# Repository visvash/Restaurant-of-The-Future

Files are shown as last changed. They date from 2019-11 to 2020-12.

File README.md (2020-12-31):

# Restaurant-of-The-Future
Restaurant of the Future: <a href="https://www.facebook.com/marsiitr/videos/214354466310067/">Facebook</a> / <a href = "https://www.youtube.com/watch?v=dR3jsaHACXw">Youtube</a>
## The Waiter Robot
> Hello,
> I have Re-designed an improved version of the robotic waiter, capable of traversing in a restaurant <b>autonomously</b> with a 3WD.
> I applied a Lead-screw based mechanism to Al-extrusions to carry and transfer <b>payloads</b> up to 10kg to variable platforms.
> It has incorporated general curve navigation with the help of encoder coupled motor and PID controller for navigation.
---
## Mechanical Design
Design: ROTF Robot<br>
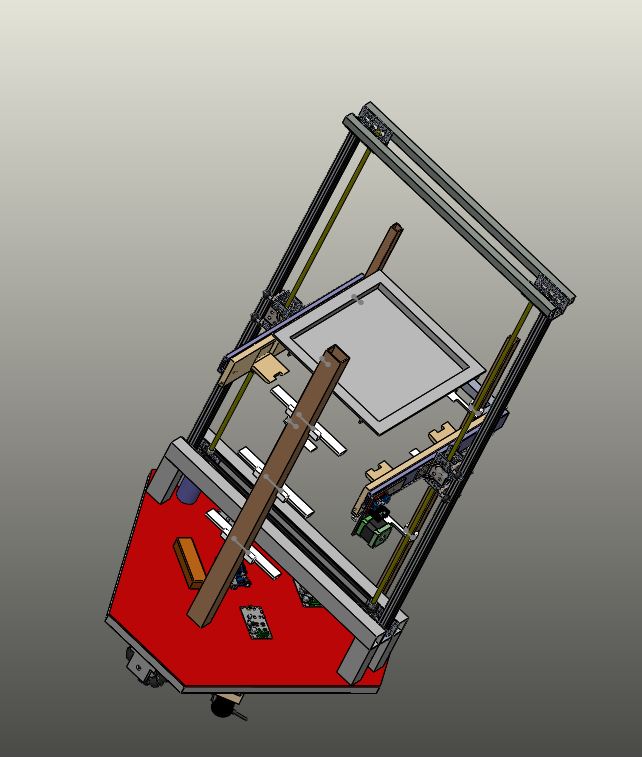
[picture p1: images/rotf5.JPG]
<br>
3 Wheel Omni Drive For Traversing<br>
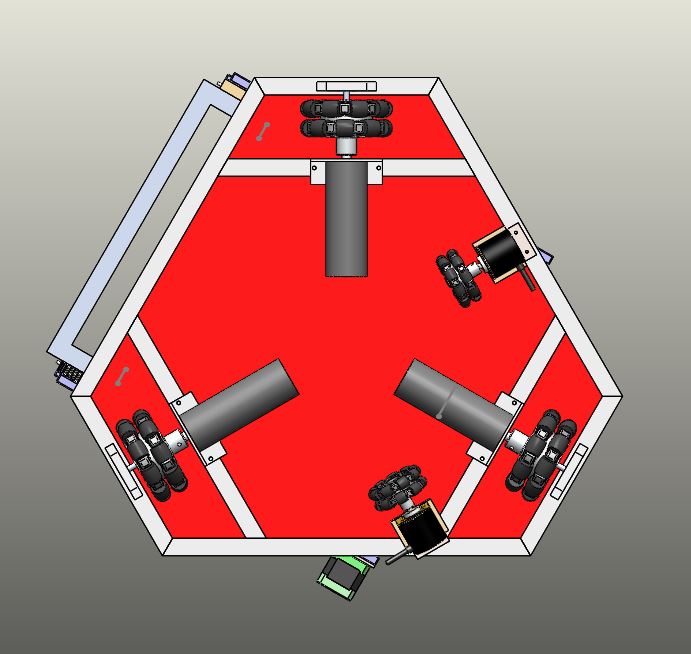
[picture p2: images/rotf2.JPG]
<br>
Extrusion Rails Using Lead-Screw Mechanism<br>
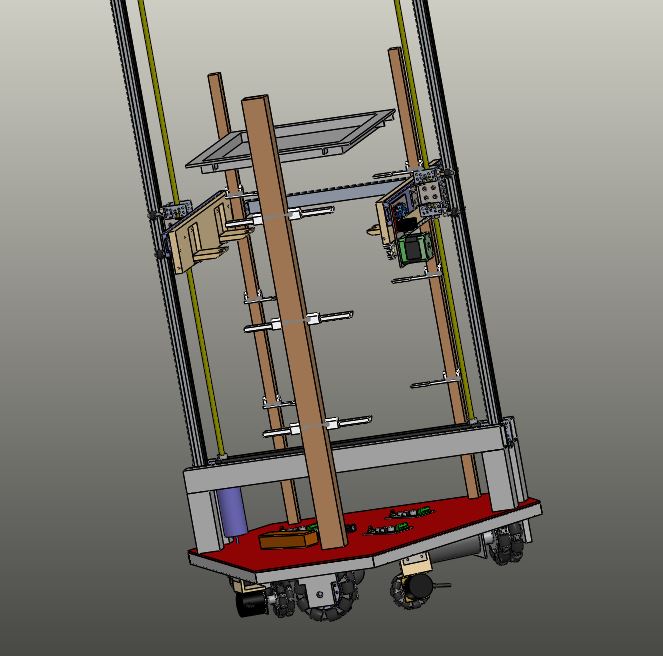
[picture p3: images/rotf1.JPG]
<br>
# Electronics and control
## Process brief
<ol>
<li>Image Input from the overhead cameras on the restaurant are processed and path is planned using Image Processing and Dijkstra Algorithm.</li>
<li>Path send to Arduino using Wifi Module</li>
<li>Omni chasis based traversal on the given path of the bot to reach the desired table.</li>
<li>Chatbot starts interacting with the the customer and takes the order while recognising face and emotion of the customer.</li>
<li>After taking order, Bot traverses back to the initial position, waits for the order to be kept on its serving trays.</li>
<li>Bot traverses back to the customer on the same path and serves using a 3-tray serving mechanism</li>
</ol>

### Path Planning and Navigation
<ol>
<li><a href =" ">Image</a> is resized to (300 * 300) pixels (<a href = " ">sample resized</a>) and edge detection is deployed on grey image (<a href = " ">sample</a>).</li>
<li>Closed objects are assigned white pixel value. Fractal concept deployed for the same(<a href = " ">sample</a>).</li>
<li>Image is smoothened(<a href = " ">sample</a>).</li>
<li>Divided into a (n*n) grid with grid size (d*d), here n = 30, d= 10 (<a href = " ">sample Grids.txt</a>). </li>
<li>Each grid is declared as an obstacle(value =0) or a path(value =1) depending of the threshold value of the white pixel count.</li>
<li>Grid generated is written in a file and is the input to the shortest path planning - Dijkstra Algorithm(<a href = " ">src code</a>). Each unit of the grid in considered as the vertic and adajent vertics are analysed of each unit to generate a matrix of all vertices. </li>
<li>"Srcdest.txt" file stores the planned path in the form of vertices to traverse on(<a href = " ">sample</a>).</li>
<li>Path string, for instance R2F2B1L1, meaning to move 2 step to the right, 2 step forward, 1 step backward, 1 step Left, is generated by reading vertices.  </li>
<li>Path string is send using the urllib library of python on the url of the esp8266 Wifi module, obtained by connecting PC and Module on the same network.</li>
</ol>
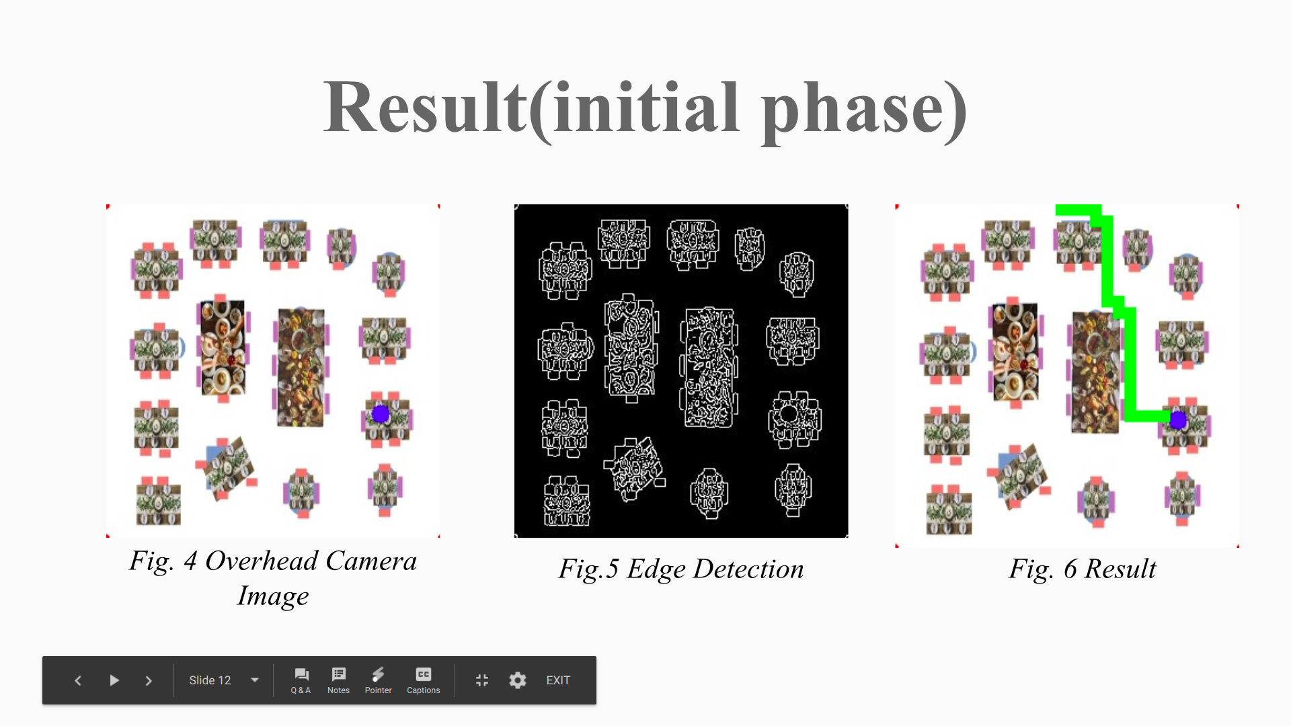
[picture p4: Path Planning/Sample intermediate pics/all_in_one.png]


### Omni chasis based motion control
<ol>
<li>Path is received using an ESP module in form of string giving units of motion in each direction. The end of path is detected by adding a letter 'e' at end of each string.</li>
<li>Each unit length of string is mapped with some unit on ground using an encoder.</li>
<li>A gyro and PID is used to avoid any rotation about its axis. Encoders and PID are used to avoid any drift.</li>
<li>Once reached the destination, it sends a signal to the head and head motion starts.</li>
<li>After getting signal from the head a "reverse" function reverses the string and adds an 'e' at the end to make the bot retrace the path back.</li>
<li>Cytron motor drivers are used for all three motors of the chassis.</li>
</ol>

### Interaction Aspect
Raspberry Pi act as a central processing system for the bot to recognise customers face and align the head accordingly using servo motors, greet and take order using Chatbot API.

### 3-Tray Serving Mechanism
<ol>
<li>After reaching the customer in mode 2, the tray motion gets activated.</li>
<li>The lifting mechanism uses dc motors and encoders, whereas the front-back motion uses stepper motor.</li>
<li>Using encoders we map the units with distance it has to traverse to reach each of the trays.</li>
<li>On reaching the tray, the front-back mechanism gets activated.</li>
<li>The number of units the stepper have to move in front and back is mapped using the standard Stepper motor library.</li>
<li>The lifting mechanism is carried by DC motors and Cytron motor driver whereas the front-back motion is supported by the stepper motors and the NEX motor driver.</li>
</ol>

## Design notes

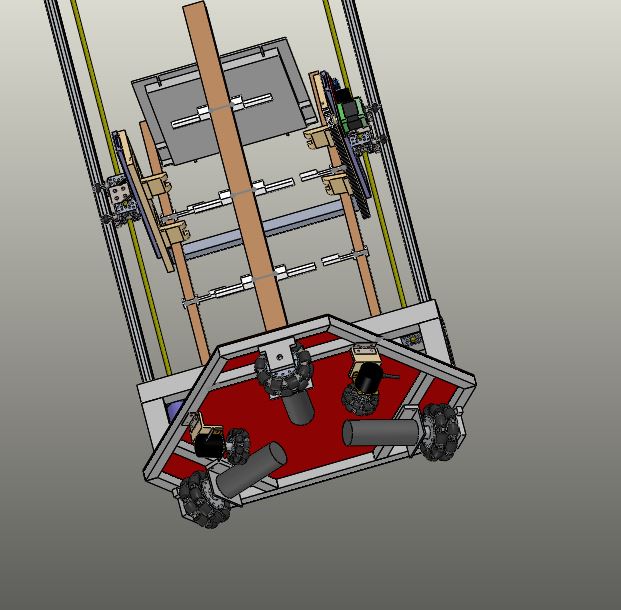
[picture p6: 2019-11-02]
images/rotf6.JPG

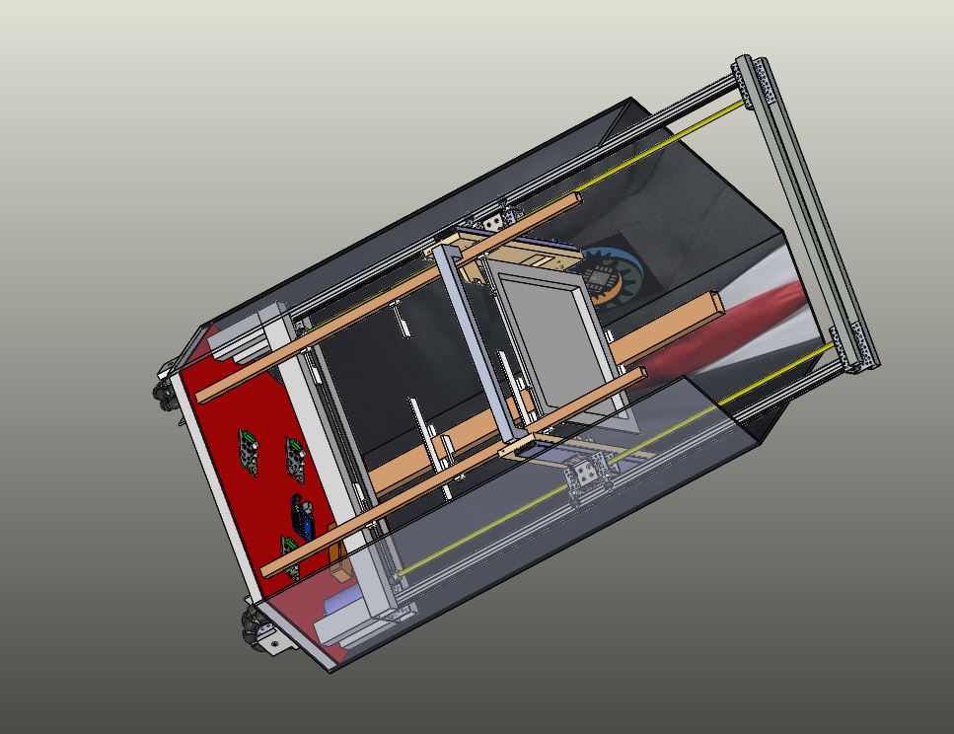
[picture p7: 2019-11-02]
images/rotf7.JPG

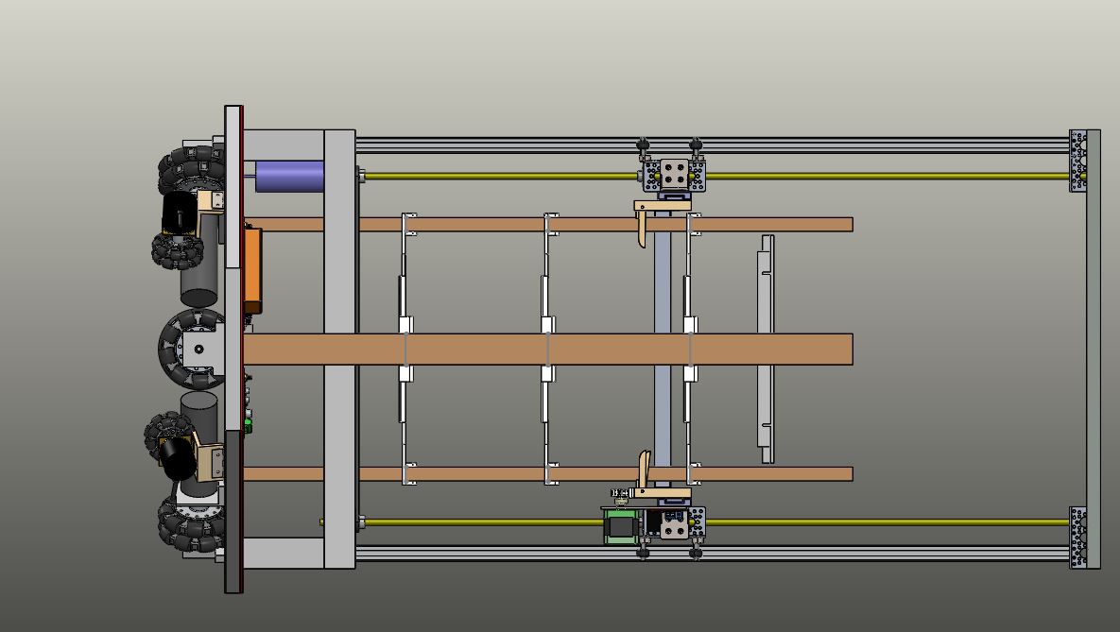
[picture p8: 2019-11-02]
images/rotf4.JPG

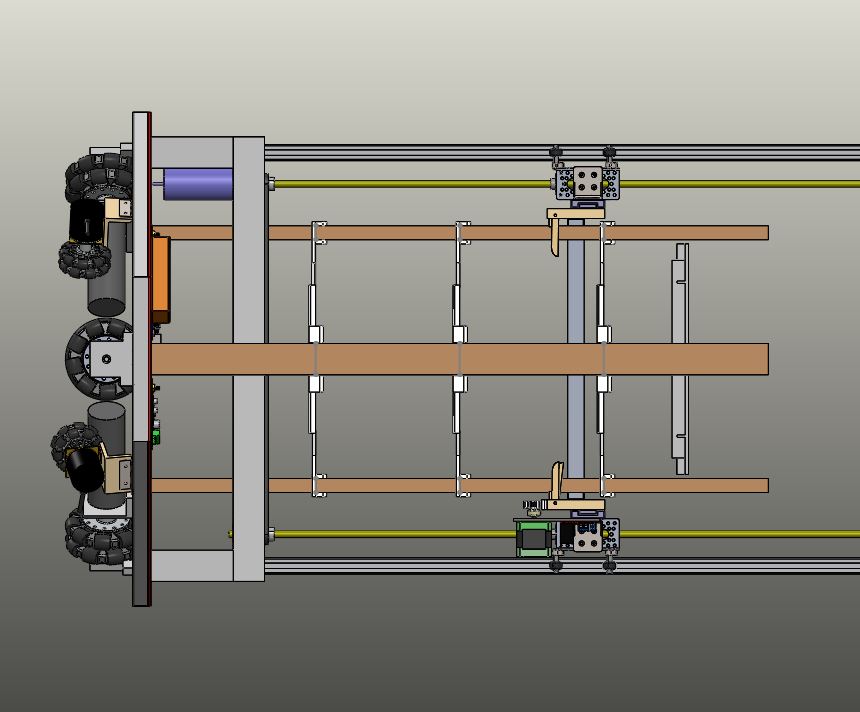
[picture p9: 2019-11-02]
images/rotf3.JPG

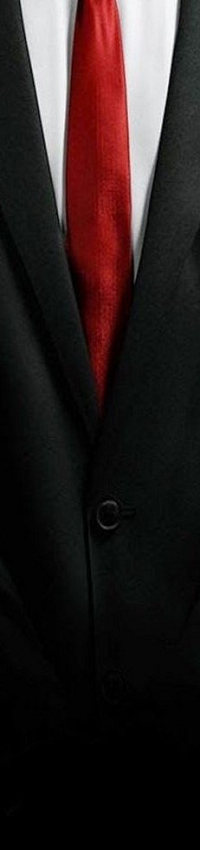
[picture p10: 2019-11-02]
ROTFnew/row-1-col-2.png

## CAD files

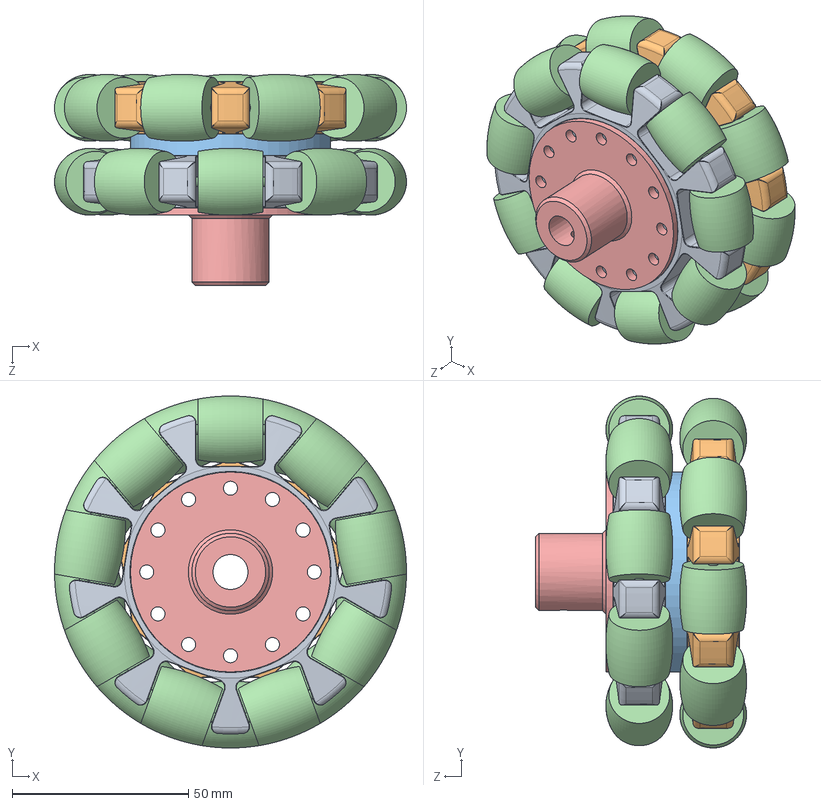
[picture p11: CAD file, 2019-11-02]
ROTFnew/OmniChasssis/OmniWheel/banhxe.SLDASM
100.0 x 100.0 x 60.0 mm
omniwheel_1
omniwheel_2
Part1^banhxe
roller x 18
Part3^banhxe

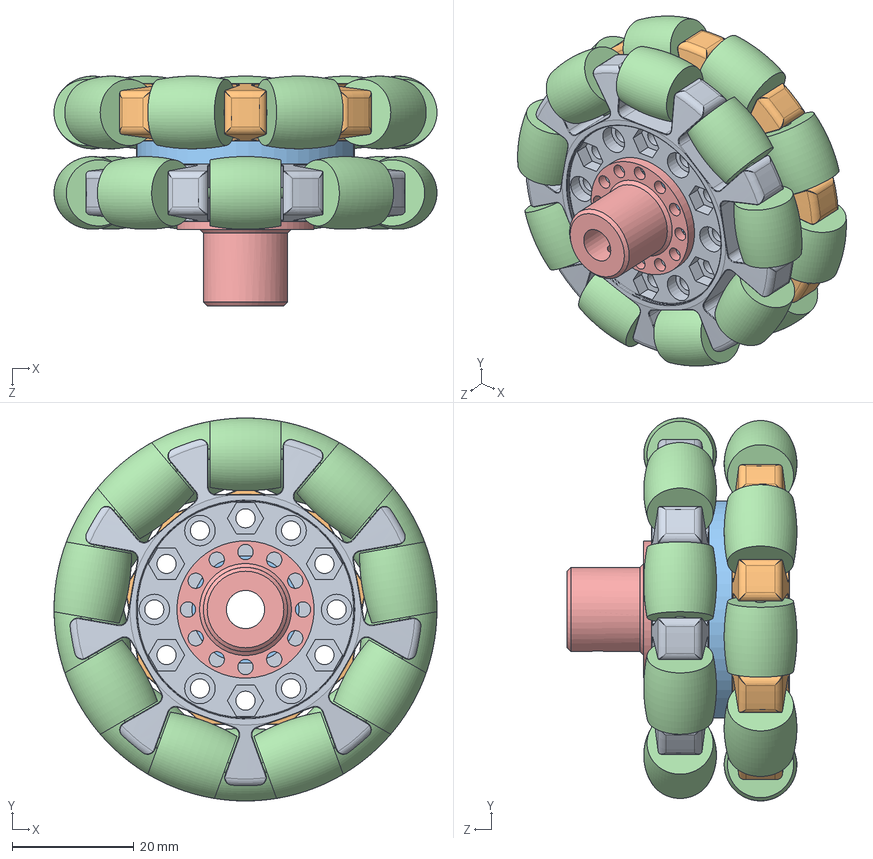
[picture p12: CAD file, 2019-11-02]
ROTFnew/OmniChasssis/OmniWheel_Encoder/banhxe.SLDASM
63.0 x 63.0 x 37.8 mm
omniwheel_1
omniwheel_2
Part1^banhxe
roller x 18
Part3^banhxe

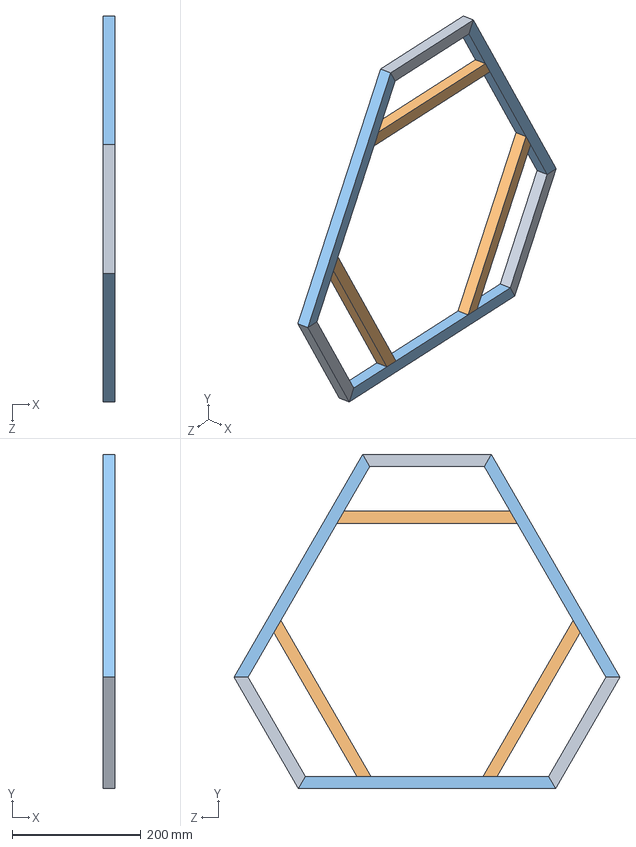
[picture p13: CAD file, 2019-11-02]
ROTFnew/OmniChasssis/OmniFrame.SLDASM
19.0 x 519.6 x 600.0 mm
Channel_200mm x 3
Channel_280mm x 3
Channel_400mm x 3

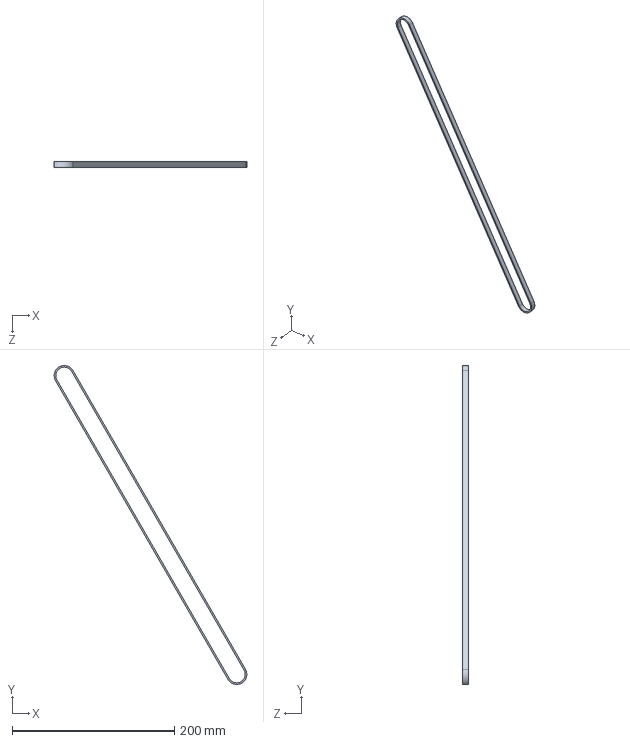
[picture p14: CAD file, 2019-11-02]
ROTFnew/Belt1-4.sldprt
237.9 x 393.7 x 7.00 mm

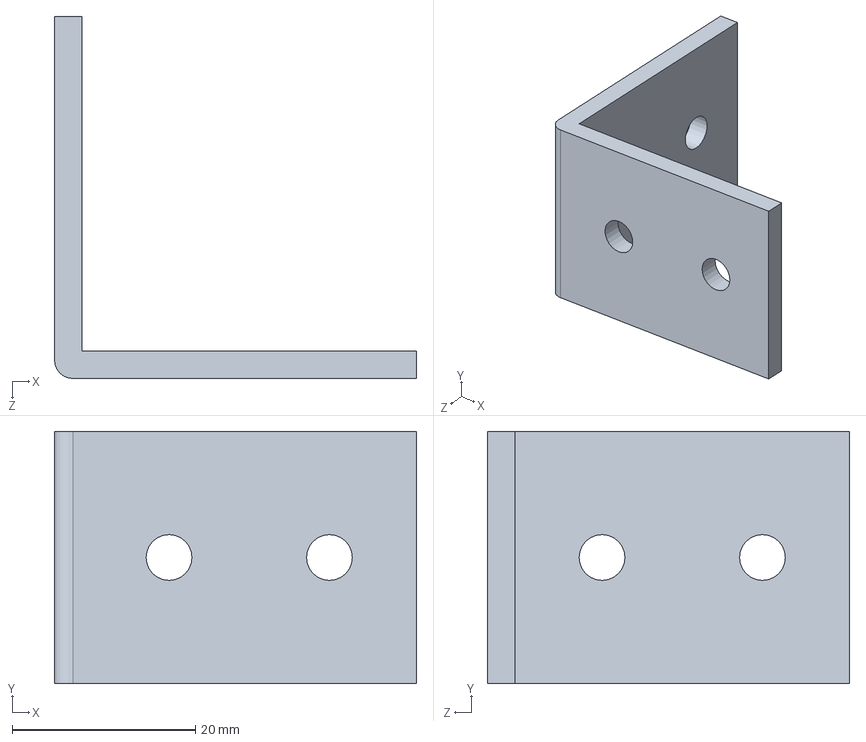
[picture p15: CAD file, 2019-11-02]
ROTFnew/Body/l mount.SLDPRT
39.5 x 27.5 x 39.5 mm

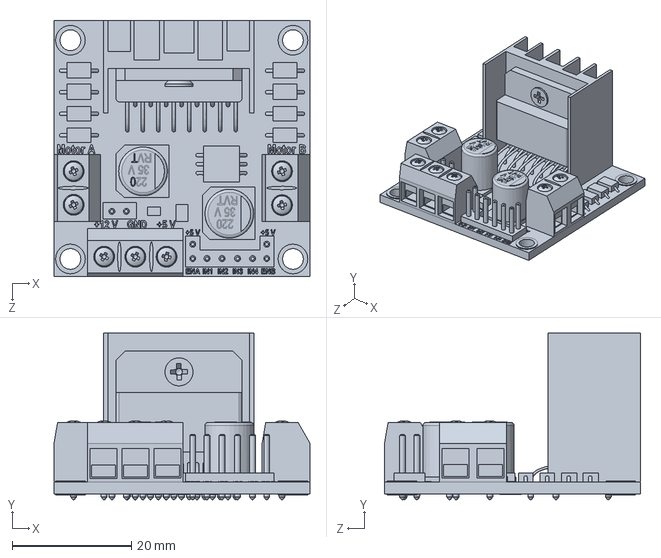
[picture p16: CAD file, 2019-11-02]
ROTFnew/electronics/L298N Stepper Motor Driver.SLDPRT
43.0 x 28.0 x 43.0 mm

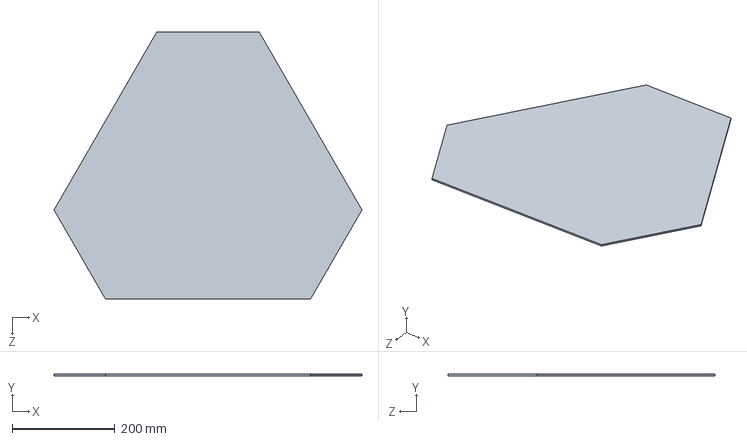
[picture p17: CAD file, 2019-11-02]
ROTFnew/OmniChasssis/Omni_Plate.SLDPRT
600.0 x 3.00 x 519.6 mm

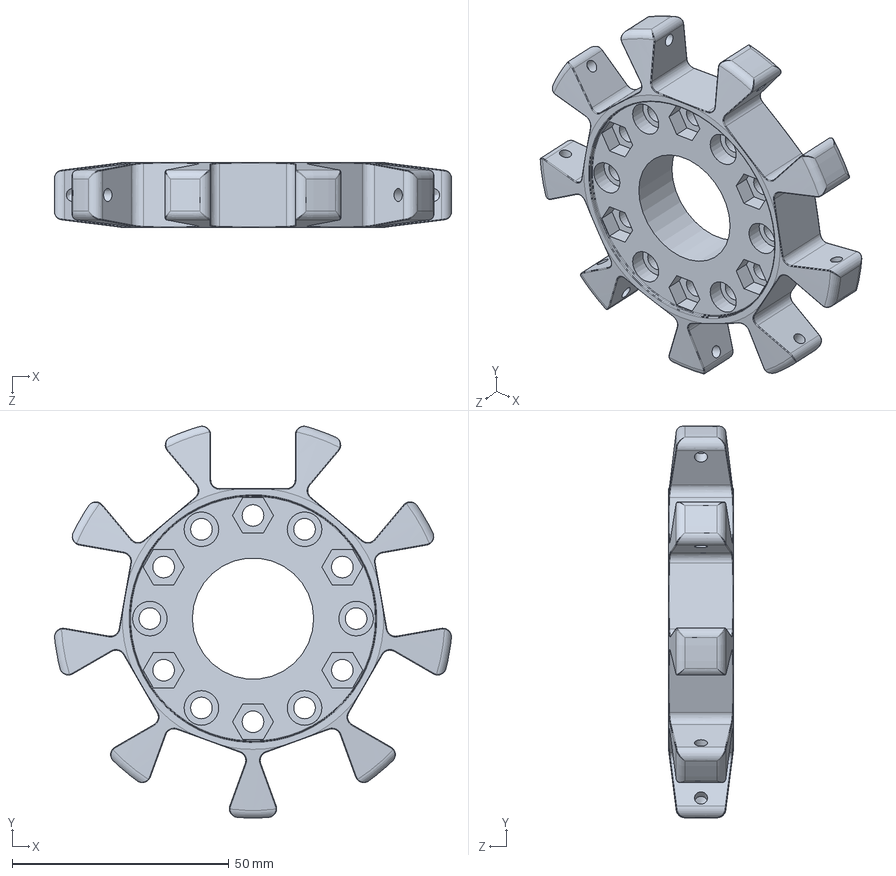
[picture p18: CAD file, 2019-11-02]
ROTFnew/OmniChasssis/OmniWheel/omniwheel_1.SLDPRT
91.6 x 90.4 x 15.0 mm

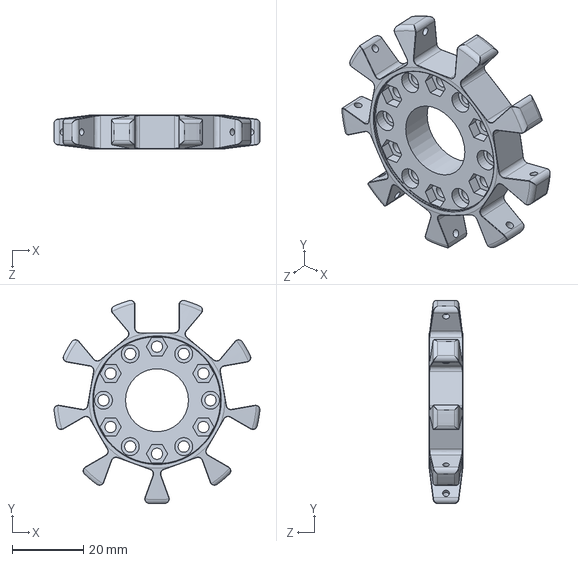
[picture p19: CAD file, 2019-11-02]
ROTFnew/OmniChasssis/OmniWheel_Encoder/omniwheel_2.SLDPRT
57.7 x 57.0 x 9.46 mm

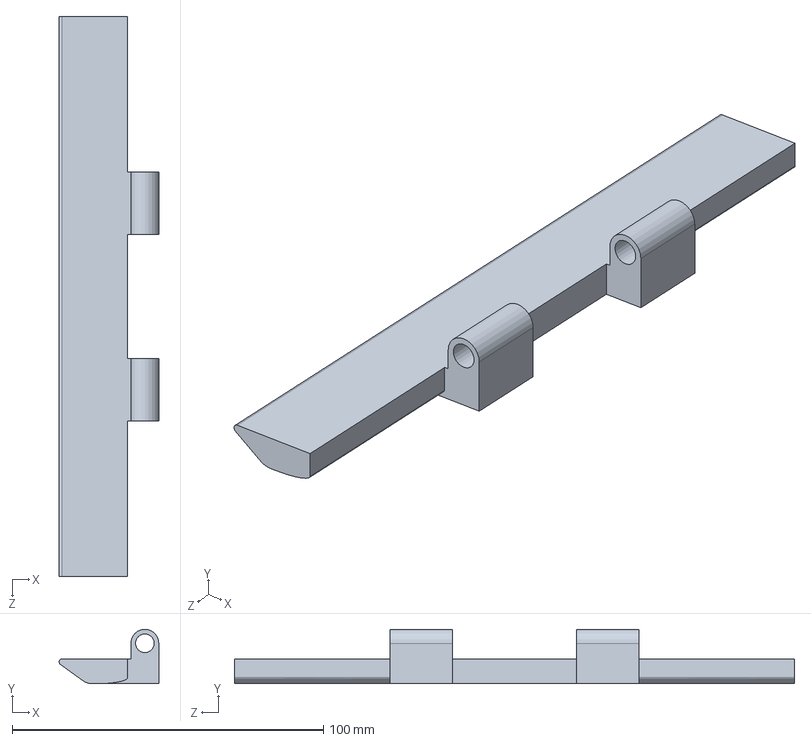
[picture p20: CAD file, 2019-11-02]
ROTFnew/Body/plate_flaps.SLDPRT
32.0 x 17.5 x 180.0 mm

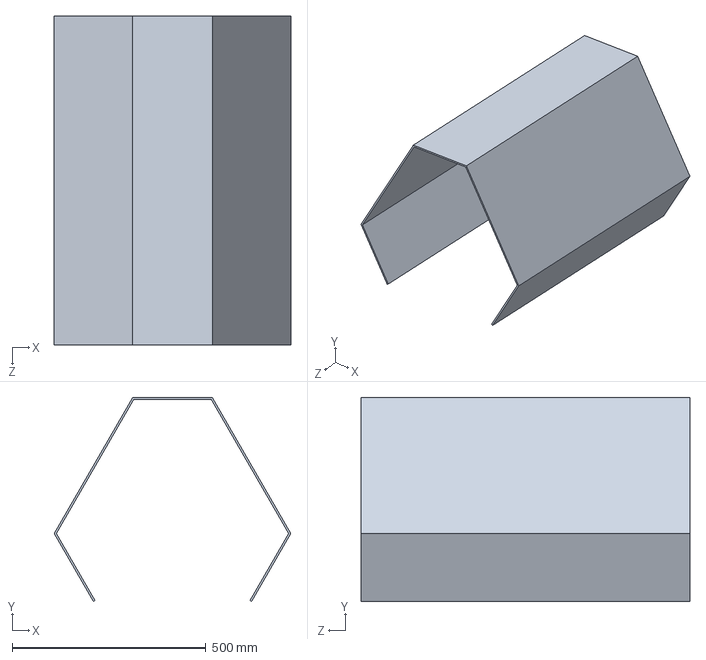
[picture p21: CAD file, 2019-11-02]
ROTFnew/cover.SLDPRT
611.5 x 527.1 x 850.0 mm

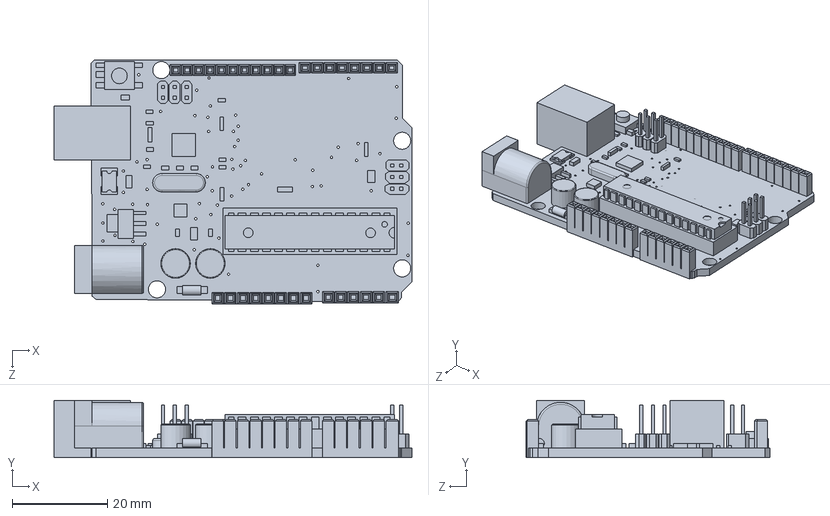
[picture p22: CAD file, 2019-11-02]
ROTFnew/electronics/Arduino UNO.SLDPRT
75.0 x 12.0 x 51.0 mm

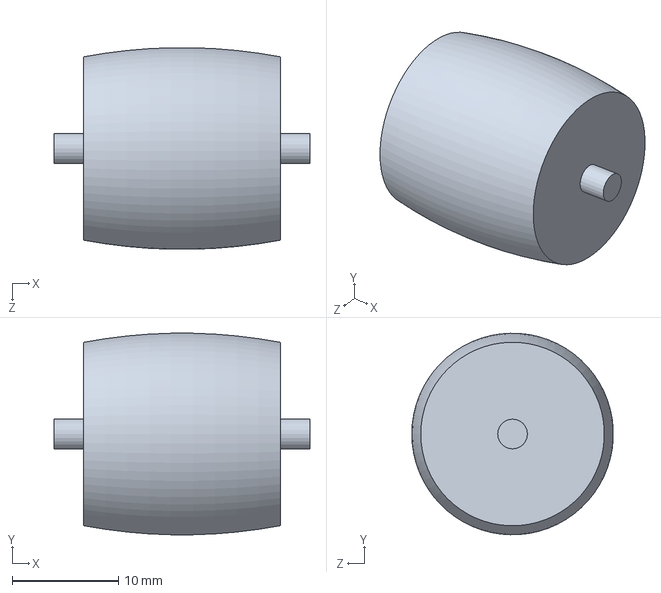
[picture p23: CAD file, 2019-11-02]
ROTFnew/OmniChasssis/OmniWheel/roller.SLDPRT
24.1 x 19.0 x 19.0 mm

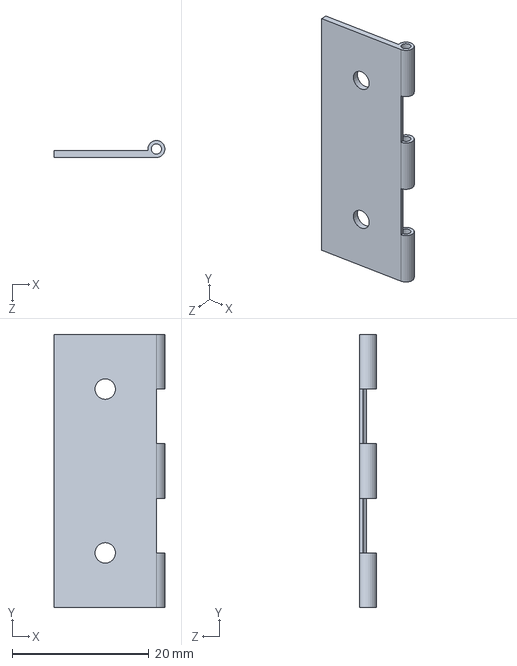
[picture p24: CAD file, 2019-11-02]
ROTFnew/OmniChasssis/Steel_hinge_1.SLDPRT
16.2 x 40.0 x 2.50 mm

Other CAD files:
ROTFnew/Body/holder.SLDPRT
ROTFnew/electronics/pin li-po.SLDPRT
ROTFnew/OmniChasssis/Channel_400mm.SLDPRT
ROTFnew/OmniChasssis/OmniWheel/Part3^banhxe.sldprt
ROTFnew/Body/10cm channel.SLDPRT
ROTFnew/Body/12inchslider1.SLDPRT
ROTFnew/Body/12inchslider2.SLDPRT
ROTFnew/Body/400cm channel.SLDPRT
ROTFnew/Body/Encoder holder.SLDPRT
ROTFnew/Body/GT2_pulley.SLDPRT
ROTFnew/Body/Gear for stepper.SLDPRT
ROTFnew/Body/Plate_holding_channel.SLDPRT
ROTFnew/Body/Rack.SLDPRT
ROTFnew/Body/SMALL plate holder new mirror.SLDPRT
ROTFnew/Body/SMALL plate holder new.SLDPRT
ROTFnew/Body/Stepper Motor.SLDPRT
ROTFnew/Body/al extrusion.SLDPRT
ROTFnew/Body/angle_bracket.SLDPRT
ROTFnew/Body/lead screw links.SLDPRT
ROTFnew/Body/lead screws/0.5in_Bore_Pillow_Block.SLDPRT
ROTFnew/Body/lead screws/0.5in_Bottom_Clamping_Mount.SLDPRT
ROTFnew/Body/lead screws/1in_Bottom_Clamping_Mount.SLDPRT
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

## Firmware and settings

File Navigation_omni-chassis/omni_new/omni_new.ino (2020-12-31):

//#include <SoftwareSerial.h>
//SoftwareSerial Serial1(8,9);//rx,tx
#include "I2Cdev.h"
#include "MPU6050_6Axis_MotionApps20.h"
#if I2CDEV_IMPLEMENTATION == I2CDEV_ARDUINO_WIRE
#include "Wire.h"
#endif
MPU6050 mpu;
#define OUTPUT_READABLE_YAWPITCHROLL

bool dmpReady = false;  // set true if DMP init was successful
uint8_t mpuIntStatus;   // holds actual interrupt status byte from MPU
uint8_t devStatus;      // return status after each device operation (0 = success, !0 = error)
uint16_t packetSize;    // expected DMP packet size (default is 42 bytes)
uint16_t fifoCount;     // count of all bytes currently in FIFO
uint8_t fifoBuffer[64]; // FIFO storage buffer

Quaternion q;           // [w, x, y, z]         quaternion container
VectorInt16 aa;         // [x, y, z]            accel sensor measurements
VectorInt16 aaReal;     // [x, y, z]            gravity-free  sensor measurements
VectorInt16 aaWorld;    // [x, y, z]            world-frame accel sensor measurements
VectorFloat gravity;    // [x, y, z]            gravity vector
float euler[3];         // [psi, theta, phi]    Euler angle container
float ypr[3];           // [yaw, pitch, roll]   yaw/pitch/roll container and gravity vector

// packet structure for InvenSense teapot demo
uint8_t teapotPacket[14] = { '$', 0x02, 0,0, 0,0, 0,0, 0,0, 0x00, 0x00, '\r', '\n' };

int Delay = 1000;
int mld=7, mrd=34, mfd=35;
int ml=6, mr=12, mf=11;
int pi_in=47, pi_out=48, p_in=50, p_out=8;
float PWMl=140, PWMr=140, PWMf=150;
//int PWM=160;
int sf=0,sr=0,sl=0;
float kpy=5, kdy=2.3, kpx=3.5, kdx=1.8;
float Error=0, dError=0, pError=0, correction=0;
int Rotations=400;
int n1 = 3;
volatile long vpr=0, vpf=0;
String path="";
String retrace="";
char ch="";
int n=0;
int time1 = 0;
int initialPosition = 0;
int angle = 0, base = 0;
int value=initialPosition;
int k=0;
int Mode=0;
const int PinBF = 3;
// Used for reading DT signal
const int PinAF = 2;
const int PinAR = 18, PinBR = 19;
// Used for the push button switch
//const int PinSW = 8;

// Keep track of last rotary value
//long Count = 0;

// ------------------------------------------------------------------
// INTERRUPT     INTERRUPT     INTERRUPT     INTERRUPT     INTERRUPT
// ------------------------------------------------------------------

void ai0F() {
  // ai0 is activated if DigitalPin nr 2 is going from LOW to HIGH
  // Check pin 3 to determine the direction
  if(digitalRead(PinAF)==LOW) {
    vpf++;
  }
  else{
    vpf--;
  }
}
   
  void ai1F() {
  // ai0 is activated if DigitalPin nr 3 is going from LOW to HIGH
  // Check with pin 2 to determine the direction
  if(digitalRead(PinBF)==LOW) {
    vpf--;
  }
  else{
    vpf++;
  }
}

void ai0R() {
  // ai0 is activated if DigitalPin nr 2 is going from LOW to HIGH
  // Check pin 3 to determine the direction
  if(digitalRead(PinAR)==LOW) {
    vpr++;
  }
  else{
    vpr--;
  }
}
   
void ai1R() {
  // ai0 is activated if DigitalPin nr 3 is going from LOW to HIGH
  // Check with pin 2 to determine the direction
  if(digitalRead(PinBR)==LOW) {
    vpr--;
  }
  else{
    vpr++;
  }
}



void setup() {
  // put your setup code here, to run once:
  Serial.begin(9600);
  #if I2CDEV_IMPLEMENTATION == I2CDEV_ARDUINO_WIRE
        Wire.begin();
        Wire.setClock(400000); // 400kHz I2C clock. Comment this line if having compilation difficulties
    #elif I2CDEV_IMPLEMENTATION == I2CDEV_BUILTIN_FASTWIRE
        Fastwire::setup(400, true);
    #endif
  while (!Serial); 
   Serial.println(F("Initializing I2C devices..."));
    mpu.initialize();
//    pinMode(INTERRUPT_PIN, INPUT);

    // verify connection
    Serial.println(F("Testing device connections..."));
    Serial.println(mpu.testConnection() ? F("MPU6050 connection successful") : F("MPU6050 connection failed"));

    // wait for ready
//    Serial.println(F("\nSend any character to begin DMP programming and demo: "));
//    while (Serial.available() && Serial.read()); // empty buffer
//    while (!Serial.available());                 // wait for data
//    while (Serial.available() && Serial.read()); // empty buffer again

    // load and configure the DMP
    Serial.println(F("Initializing DMP..."));
    devStatus = mpu.dmpInitialize();

    // supply your own gyro offsets here, scaled for min sensitivity
    mpu.setXGyroOffset(220);
    mpu.setYGyroOffset(76);
    mpu.setZGyroOffset(-85);
    mpu.setZAccelOffset(1788); // 1688 factory default for my test chip

    // make sure it worked (returns 0 if so)
    if (devStatus == 0) {
        // turn on the DMP, now that it's ready
        Serial.println(F("Enabling DMP..."));
        mpu.setDMPEnabled(true);

        // enable Arduino interrupt detection
        Serial.println(F("Enabling interrupt detection (Arduino external interrupt 0)..."));
        //attachInterrupt(digitalPinToInterrupt(INTERRUPT_PIN), dmpDataReady, RISING);
        mpuIntStatus = mpu.getIntStatus();

        // set our DMP Ready flag so the main loop() function knows it's okay to use it
        Serial.println(F("DMP ready! Waiting for first interrupt..."));
        //dmpReady = true;

        // get expected DMP packet size for later comparison
        packetSize = mpu.dmpGetFIFOPacketSize();
    } else {
        // ERROR!
        // 1 = initial memory load failed
        // 2 = DMP configuration updates failed
        // (if it's going to break, usually the code will be 1)
        Serial.print(F("DMP Initialization failed (code "));
        Serial.print(devStatus);
        Serial.println(F(")"));
    }

  pinMode(p_in, INPUT);
  pinMode(p_out, OUTPUT);
  pinMode(pi_in, INPUT);
  pinMode(pi_out, OUTPUT);
  pinMode(mld, OUTPUT);
  pinMode(mrd, OUTPUT);
  pinMode(mfd, OUTPUT);
  pinMode(ml, OUTPUT);
  pinMode(mr, OUTPUT);
  pinMode(mf, OUTPUT);
  digitalWrite(p_out, HIGH);
  digitalWrite(pi_out, LOW);

  pinMode(PinAF, INPUT_PULLUP);
  pinMode(PinBF, INPUT_PULLUP);
  pinMode(PinAR, INPUT_PULLUP);
  pinMode(PinBR, INPUT_PULLUP);

  attachInterrupt(1,ai0F,RISING);
  attachInterrupt(0,ai1F,RISING);
  attachInterrupt(4,ai0R,RISING);
  attachInterrupt(5,ai1R,RISING);

  Serial2.begin(9600);
  while(!Serial2.available()){
    Serial.println("waiting");
  }
  while(Serial2.available()){
    char ch1 = Serial2.read();
   Serial.print(ch1);
    path = path+ch1;
  }

  Serial3.begin(9600);
  
  Serial.println(path);

  int t = millis();
  while(millis()-t<20000){
    Err();
    Serial.println(millis()-t);
    Serial.print("angle: ");
    Serial.println(angle);
  }
  base = angle;
  
}

void Err(){
  mpuIntStatus = mpu.getIntStatus();

    // get current FIFO count
    fifoCount = mpu.getFIFOCount();

    // check for overflow (this should never happen unless our code is too inefficient)
    if ((mpuIntStatus & 0x10) || fifoCount == 1024) {
        // reset so we can continue cleanly
        mpu.resetFIFO();
        Serial.println(F("FIFO overflow!"));

    // otherwise, check for DMP data ready interrupt (this should happen frequently)
    } else if (mpuIntStatus & 0x02) {
        // wait for correct available data length, should be a VERY short wait
        while (fifoCount < packetSize) fifoCount = mpu.getFIFOCount();

        // read a packet from FIFO
        mpu.getFIFOBytes(fifoBuffer, packetSize);
        
        // track FIFO count here in case there is > 1 packet available
        // (this lets us immediately read more without waiting for an interrupt)
        fifoCount -= packetSize;

        #ifdef OUTPUT_READABLE_QUATERNION
            // display quaternion values in easy matrix form: w x y z
            mpu.dmpGetQuaternion(&q, fifoBuffer);
            Serial.print("quat\t");
            Serial.print(q.w);
            Serial.print("\t");
            Serial.print(q.x);
            Serial.print("\t");
            Serial.print(q.y);
            Serial.print("\t");
            Serial.println(q.z);
        #endif

        #ifdef OUTPUT_READABLE_EULER
            // display Euler angles in degrees
            mpu.dmpGetQuaternion(&q, fifoBuffer);
            mpu.dmpGetEuler(euler, &q);
//            Serial.print("euler\t");
//            Serial.print(euler[0] * 180/M_PI);
//            Serial.print("\t");
//            Serial.print(euler[1] * 180/M_PI);
//            Serial.print("\t");
//            Serial.println(euler[2] * 180/M_PI);
        #endif

        #ifdef OUTPUT_READABLE_YAWPITCHROLL
            // display Euler angles in degrees
            mpu.dmpGetQuaternion(&q, fifoBuffer);
            mpu.dmpGetGravity(&gravity, &q);
            mpu.dmpGetYawPitchRoll(ypr, &q, &gravity);
//            Serial.print("ypr\t");
//            Serial.print(ypr[0] * 180/M_PI);
//            Serial.print("\t");
//            Serial.print(ypr[1] * 180/M_PI);
//            Serial.print("\t");
//            Serial.println(ypr[2] * 180/M_PI);
        #endif
        angle = ypr[0]*180/M_PI;
    }   
}



int mod(int value){
  if(value<0){
    return -1*value;
  }
  return value;
}

void Forward(){
  digitalWrite(mld,HIGH);
  digitalWrite(mrd,LOW);
//  sr = 0;
//  sl = 0;
//  sf = 0;
//  while(sr<PWMr && sl<PWMl){
//    sr += 20;
//    sl += 20;
//    //sf += 0;
//    analogWrite(ml,sl);
//    analogWrite(mr,sr);
//    analogWrite(mf,sf); 
//    delay(Delay);
//  }

  Err();
  Error = angle-base;
  dError = Error - pError;
  correction = kpy*pError + kdy*dError;
  Serial.print("correction=");
  Serial.println(correction);
  sl=PWMl+correction+15;
  sr=PWMr-correction;
  sf=0;
  analogWrite(mf,mod(sf));
  analogWrite(ml,mod(sl));
  analogWrite(mr,mod(sr));
  Serial.print(sl);
  Serial.print(" ");
  Serial.print(sr);
  Serial.print(" ");
  Serial.println(sf);
  //value = vpf;
}

void Left(){
  digitalWrite(mld,HIGH);
  digitalWrite(mrd,HIGH);
  
  digitalWrite(mfd,LOW);
//  sr = 0;
//  sl = 0;
//  sf = 0;
//  while(sr<PWMr && sl<PWMl){
//    sr += 20;
//    sl += 20;
//    sf += 20;
//    analogWrite(ml,sl);
//    analogWrite(mr,sr);
//    analogWrite(mf,sf); 
//    delay(Delay);
//  }

  Err();
  Error = angle-base;
  dError = Error - pError;
  correction = kpx*pError + kdx*dError;
  Serial.print("Error=");
  Serial.println(Error);
  sl = PWMl+correction-40;
  sr = PWMr+correction-40;
  sf = PWMf-correction-40;
  pError = Error;

  Serial.print(sl);
  Serial.print(" ");
  Serial.print(sr);
  Serial.print(" ");
  Serial.println(sf);
  analogWrite(mf,mod(sf));
  analogWrite(ml,mod(sl));
  analogWrite(mr,mod(sr));
  //value = vpf;
}

void Right(){
  digitalWrite(mld,LOW);
  digitalWrite(mrd,LOW);
  digitalWrite(mfd,HIGH);
//  sr = 0;
//  sl = 0;
//  sf = 0;
//  while(sr<PWMr && sl<PWMl){
//    sr += 20;
//    sl += 20;
//    sf += 20;
//    analogWrite(ml,sl);
//    analogWrite(mf,sf);
//    analogWrite(mr,sr);
//     
//    delay(Delay);
//  }

  Err();
  Error = angle-base;
  dError = Error - pError;
  correction = kpx*pError + kdx*dError;
  
  sl = PWMl-correction-40;
  sr = PWMr-correction-40;
  sf = PWMf+correction-50;
  pError = Error;
  Serial.print("Error=");
  Serial.println(Error);
  Serial.print(sl);
  Serial.print(" ");
  Serial.print(sr);
  Serial.print(" ");
  Serial.println(sf);
  analogWrite(ml,mod(sl));
  analogWrite(mf,mod(sf));
  analogWrite(mr,mod(sr));
  
  //value = vpf;
}

void Backward(){
  digitalWrite(mld,LOW);
  digitalWrite(mrd,HIGH);
//  sr = 0;
//  sl = 0;
//  sf = 0;
//  while(sr<PWMr && sl<PWMl){
//    sr += 20;
//    sl += 20;
//    //sf += 10;
//    analogWrite(ml,sl);
//    analogWrite(mf,sf);
//    analogWrite(mr,sr);
//    delay(Delay);
//  }
  Err();
  Error = angle-base;
  dError = Error - pError;
  correction = kpy*pError + kdy*dError;
  Serial.print("Error=");
  Serial.println(Error);
  sr=PWMr+correction;
  sl=PWMl-correction+20;
  sf = 0;
  Serial.print(sl);
  Serial.print(" ");
  Serial.print(sr);
  Serial.print(" ");
  Serial.println(sf);
  
  analogWrite(ml,mod(sl));
  analogWrite(mf,mod(sf));
  analogWrite(mr,mod(sr));
  
  //value = vpf;
}

void Stop(){
  sr = PWMr;
  sl = PWMl;
  
  while(sr>0 && sl>0){
    sr -= 20;
    sl -= 20;
    if(sf>0){
      sf -= 20;
    }
    analogWrite(ml,sl);
    analogWrite(mf,sf);
    analogWrite(mr,sr);    
    delay(50);
  }
  
  sl=0;
  sr=0;
  sf=0;
  analogWrite(mf,sf);
  analogWrite(ml,sl);
  analogWrite(mr,sr);
  delay(Delay);
}


void invert(String temp){
  int N = temp.length();
  for(int i=0; i<N/2; i++){
    char ch1 = temp[i];
    char ch2 = temp[N-i-1];
    temp[i] = ch2;
    temp[N-i-1] = ch1;
  }
  retrace = temp;
}


void turn(int val){
  if(val==0){
    
    digitalWrite(mld,HIGH); 
    digitalWrite(mrd,HIGH);
    digitalWrite(mfd,HIGH);
    sl = 100;
    sf = 120;
    sr = 100;
    analogWrite(ml, sl);
    analogWrite(mr, sr);
    analogWrite(mf, sf);
    while(mod(angle)>mod(base+4)){
      Err();
      Serial.println(angle-base);
    }
  }
  else if(val<0){
//    val = mod(val);
    digitalWrite(mld,HIGH);
    digitalWrite(mrd,HIGH);
    digitalWrite(mfd,HIGH);
    sl = 100;
    sf = 120;
    sr = 100;
    analogWrite(ml, sl);
    analogWrite(mr, sr);
    analogWrite(mf, sf);
    while(angle-base>val+4){
      Err();
      Serial.println(angle-base);
    }
  }
  else if(val>0){
    digitalWrite(mld,LOW);
    digitalWrite(mrd,LOW);
    digitalWrite(mfd,LOW);
    sl = 100;
    sf = 120;
    sr = 100;
    analogWrite(ml, sl);
    analogWrite(mr, sr);
    analogWrite(mf, sf);
    while(mod(angle-base)<val-4){
      Err();
      Serial.println(mod(angle-base));
    }
  }
  Stop();
//  delay(500);
  Err();
  Serial.println(angle-base);
}




void Retrace(){
  k=0;
  while(Mode==1 || Mode==3){
    if(retrace.charAt(k)==' '){
      k++;
    }
    ch = retrace.charAt(k);
    k++;
    n = (int)retrace.charAt(k);
    n = n-48;  
    k++;
    if((int)retrace.charAt(k)>=48 && (int)retrace.charAt(k)<=57){
      n = n*10 + (int)retrace.charAt(k)-48;
      k++;
    }
    
    if(ch=='F'){
      initialPosition = vpr;
      value = initialPosition;
      Serial.println("Forward");
      while(mod(value-initialPosition)<=Rotations*(n*n1)){
        Forward();
        //delay(30);
        Serial.println(mod(value-initialPosition));
        value = vpr;
        //Serial.println(value);
      }
      Stop();
      //delay(500);
    }
      
    if(ch=='R'){
      sf = PWMf;
      Serial.println("right");
      initialPosition = vpf;
      value = initialPosition;
      while(mod(value-initialPosition)<=Rotations*(n*n1)){
        Right();
        //delay(30);
        Serial.println(mod(value-initialPosition));
        value = vpf;
      }
      Stop();
      //delay(500);
    }
      
    if(ch=='L'){
      sf = PWMf;
      Serial.println("Left");
      initialPosition = vpf;
      value = initialPosition;
      while(mod(value-initialPosition)<=Rotations*(n*n1)){
        Left();
        //delay(30);
        Serial.println(mod(value-initialPosition));
        value = vpf;    
      }
      Stop();
      //delay(500);
    }
    if(ch=='B'){
      Serial.println("back");
      initialPosition = vpr;
      value = initialPosition;
      while(mod(value-initialPosition)<=Rotations*(n*n1)){
        Backward();
        //delay(30);
        Serial.println(mod(value-initialPosition));
        value = vpr;
        //Serial.println(value);
      }
      Stop();
//      delay(500);
    }

    if(ch=='e'){
      Stop();
      Mode++;
      retrace = "";
      k=0;
    }
  }
}


void loop() {
  
  if(path.charAt(k)==' '){
    k++;
  }
  ch = path.charAt(k);
  k++;
  n = (int)path.charAt(k);
  n = n-48;
  if((int)path.charAt(k+1)>=48 && (int)path.charAt(k+1)<=57){
    n = n*10 + (int)path.charAt(k+1)-48;
    k++; 
  }
  
  
  if(ch=='e'){
    invert(retrace);
    retrace = retrace + "e0";
  }
  
  else{
    if(n>9){
      if(ch=='F'){
        retrace = retrace + path.charAt(k) + path.charAt(k-1) + "B";
      }
      if(ch=='B'){
        retrace = retrace + path.charAt(k) + path.charAt(k-1) + "F";
      }
      if(ch=='R'){
        retrace = retrace + path.charAt(k) + path.charAt(k-1) + "L";
      }
      if(ch=='L'){
        retrace = retrace + path.charAt(k) + path.charAt(k-1) + "R";
      }
    }
    else{
      if(ch=='F'){
        retrace = retrace + path.charAt(k) + "B";
      }
      if(ch=='B'){
        retrace = retrace + path.charAt(k) + "F";
      }
      if(ch=='R'){
        retrace = retrace + path.charAt(k) + "L";
      }
      if(ch=='L'){
        retrace = retrace + path.charAt(k) + "R";
      }
    }
  }
  
  k++;
  
  //time1 = millis();
  //Serial.print(ch);
  //Serial.println(n);
  
    if(ch=='F'){
      initialPosition = vpr;
      value = initialPosition;
      Serial.println("Forward");
      while(mod(value-initialPosition)<=Rotations*(n*n1)){
        Forward();
        //delay(30);
        Serial.println(mod(value-initialPosition));
        value = vpr;
        //Serial.println(value);
      }
      Stop();
//      delay(500);
    }
      
    if(ch=='R'){
      sf = PWMf;
      Serial.println("right");
      initialPosition = vpf;
      value = initialPosition;
      while(mod(value-initialPosition)<=Rotations*(n*n1)){
        Right();
        //delay(30);
        Serial.println(mod(value-initialPosition));
        value = vpf;
      }
      Stop();
//      delay(500);
    }
      
    if(ch=='L'){
      sf = PWMf;
      Serial.println("Left");
      initialPosition = vpf;
      value = initialPosition;
      while(mod(value-initialPosition)<=Rotations*(n*n1)){
        Left();
        //delay(30);
        Serial.println(mod(value-initialPosition));
        value = vpf;    
      }
      Stop();
      delay(500);
    }
    if(ch=='B'){
      Serial.println("back");
      initialPosition = vpr;
      value = initialPosition;
      while(mod(value-initialPosition)<=Rotations*(n*n1)){
        Backward();
        //delMay(30);
        Serial.println(mod(value-initialPosition));
        value = vpr;
        //Serial.println(value);
      }
      Stop();
//      delay(500);
    }

    if(ch=='e'){
      Stop();
      //delay(Delay);
      switch(n){
        case 0:
          Serial.println("turn -90");
          turn(-90);
          if(Mode == 2){
            Serial3.println("a");
            while(!Serial3.available()){
              
            }
//            digitalWrite(p_out,LOW);
          }

          if(Mode == 0){
            digitalWrite(pi_out,HIGH);
            Serial.println("a");
            while(true){
              if(digitalRead(pi_in)==HIGH){
                Serial.println("c");
                break;  
              }
              
            }
            digitalWrite(pi_out,LOW);
            Serial.println("b");
          }
          
          turn(0);
          break;
        case 3:
          Serial.println("turn 0");
          
          if(Mode == 2){
            Serial3.println("a");
            while(!Serial3.available()){
              
            }
//            digitalWrite(p_out,LOW);
          }
//            digitalWrite(p_out,LOW);
          

          if(Mode == 0){
            digitalWrite(pi_out,HIGH);
            Serial.println("a");
            while(true){
              if(digitalRead(pi_in)==HIGH){
                Serial.println("c");
                break;  
              }
              
            }
            digitalWrite(pi_out,LOW);
            Serial.println("b");
          }
          break;
        case 2:
          Serial.println("turn 90");
          turn(90);
          if(Mode == 2){
            Serial3.println("a");
            while(!Serial3.available()){
              
            }
//            digitalWrite(p_out,LOW);
          }
          
          if(Mode == 0){
            digitalWrite(pi_out,HIGH);
            Serial.println("a");
            while(true){
              if(digitalRead(pi_in)==HIGH){
                Serial.println("c");
                break;  
              }
              
            }
            digitalWrite(pi_out,LOW);
            Serial.println("b");
          }
          turn(0);
          
          break;
        case 1:
          Serial.println("turn 180");
          turn(178);
          if(Mode == 2){
            Serial3.println("a");
            while(!Serial3.available()){
              
            }
//            digitalWrite(p_out,LOW);
          }

          if(Mode == 0){
            digitalWrite(pi_out,HIGH);
            Serial.println("a");
            while(true){
              if(digitalRead(pi_in)==HIGH){
                Serial.println("c");
                break;  
              }
              
            }
            digitalWrite(pi_out,LOW);
            Serial.println("b");
          }
          turn(0);
          break;
        
      }
      
      Serial.println(retrace);
      Mode++;
      Serial.print("Mode bret");
      Serial.println(Mode);
      Retrace();
      k=0;
      delay(Delay);
      if(Mode>3){
        path = "";
        retrace = "";
      }
    }
}

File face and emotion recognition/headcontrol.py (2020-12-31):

from RPi import GPIO
from time import sleep
import socket
import sys

s = socket.socket(socket.AF_INET, socket.SOCK_STREAM)
port = 3125
s.bind(('10.42.0.1', port))
s.listen(3)
print('socket is listening')

clk = 17
dt = 18
kd = 0
qmaxi = 18 # speed of neck rotation
qmini = 0   # encoders must be initially at this position ie origin
mp1 = 27 # motor 1 pwm
i1 = 22
i2 = 23
mp2 = 24 # servo pwm motor 2
calib = 25


GPIO.setmode(GPIO.BCM)
GPIO.setup(clk, GPIO.IN, pull_up_down=GPIO.PUD_UP)
GPIO.setup(dt, GPIO.IN, pull_up_down=GPIO.PUD_UP)
GPIO.setup(calib, GPIO.IN, pull_up_down=GPIO.PUD_UP)
GPIO.setup(mp1, GPIO.OUT)
GPIO.setup(i1, GPIO.OUT)
GPIO.setup(mp2, GPIO.OUT)
GPIO.setup(i2, GPIO.OUT)
p=GPIO.PWM(mp1, 100)
p.start(1) 
pwm=GPIO.PWM(mp2, 50)
pwm.start(1)

global clkLastState
global counter
global a
global b
global seek


counter = 0


def my_callback(channel): 
    clkState = GPIO.input(clk)
    dtState = GPIO.input(dt)
    global clkLastState
    global counter
    
    if dtState != clkState:
      counter += 1
    else:
      counter -= 1

GPIO.add_event_detect(17, GPIO.BOTH  , callback=my_callback, bouncetime=1)  # ye background me chalu h

def SetAngle(angle):
    
    duty = angle / 18 + 2
    GPIO.output(mp2, True)
    pwm.ChangeDutyCycle(duty)
    sleep(1)
    GPIO.output(mp2, False)
    pwm.ChangeDutyCycle(0)
    
def motor(x ,prerr):
        q = counter
        qx = x #mapping

        
        if  q >= qx:
          GPIO.output(i1, GPIO.LOW)
          GPIO.output(i2, GPIO.HIGH) #left ghumega
          err = abs( q - qx) / qmaxi - kd * (prerr - ( q - qx))
          p.ChangeDutyCycle(abs(err+10))
          sleep(0.1)
          p.ChangeDutyCycle(0)
          
          

        else:
          GPIO.output(i1, GPIO.HIGH)
          GPIO.output(i2, GPIO.LOW)     #right ghumega
          err = (abs(q - qx) / qmaxi)  -  kd * (prerr - ( q - qx))
          p.ChangeDutyCycle(abs(err+10))     #min duty=10
          sleep(0.1)
          p.ChangeDutyCycle(0)



while True: 

     seek = GPIO.input(calib)
     
     if seek==0:
       break
       
     if counter >= 400:
       break
       
     GPIO.output(i1, GPIO.HIGH)
     GPIO.output(i2, GPIO.LOW)
     p.ChangeDutyCycle(15)
     print(seek)

     
while True: 

     seek = GPIO.input(calib)
     
     if seek==0:
       break
       
       
     GPIO.output(i1, GPIO.LOW)
     GPIO.output(i2, GPIO.HIGH)
     p.ChangeDutyCycle(15)
     print(seek)

  
p.ChangeDutyCycle(0)

counter = 0

while True:
   c, addr = s.accept()
   print('Got connection from', addr)
   string = c.recv(1024)
   print(string)
   list_string = string.split(",")
   X = int(((list_string[0]*600)/640) -300)
   Y = int((list_string[1]*40)/480)
   emotion = str(list_string[2])
   c.close()
   i=0
   b =  X  # -300 to 300
   a =  Y  # 0 to 40
   
   prerr=b
           
   SetAngle(a)
   
   
   
   while i<5:

        zero = GPIO.input(calib)
        
        if zero == 0:
          counter = 0
                
        i=i+1
       
        motor(b ,prerr)
        
        prerr= abs(counter - b)

     
raw_input("Enter anything")


GPIO.cleanup()
